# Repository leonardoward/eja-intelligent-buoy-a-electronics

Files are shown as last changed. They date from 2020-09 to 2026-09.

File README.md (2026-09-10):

# EJA Intelligent Buoy A - Electronic Design

EJA Intelligent Buoy A - Electronic Design - [2020 Hackaday Dream Team Challenge for Conservation X Labs](https://hackaday.io/project/173457-2020-hdp-dream-team-conservation-x-labs).

Buoy A is a 141.73 mm x 54.86 mm PCB that integrates 5 main modules (ESP32, LoRa, GPS, Motor Driver and GSM/GPRS).

This repository contains the KiCad design for the PCB of the Intelligent Buoy A. It also contains the 3D models used to visualize the design in the KiCad 3D viewer.

## Context

**EJA** is a pop‑up recovery buoy for lost fishing gear. A buoy sits on the seabed
attached to a trap or net; a scheduled timer (or a command over LoRa from the
[Onboard Gateway](https://github.com/leonardoward/eja-onboard-gateway-electronics))
releases it, it floats up, and its GPS position is reported so the gear can be
recovered. **Buoy A** is the fuller variant &mdash; it adds a **TB6612FNG** motor driver
for the release actuator and an optional **SIM7600 GSM/GPRS** shield for a cellular
uplink where there is coverage. It runs the
[Buoy firmware](https://github.com/leonardoward/eja-intelligent-buoy-b-firmware).
The single‑board successor that folds this whole system onto one PCB is
[EJA M](https://github.com/leonardoward/eja-m-pcb-design).

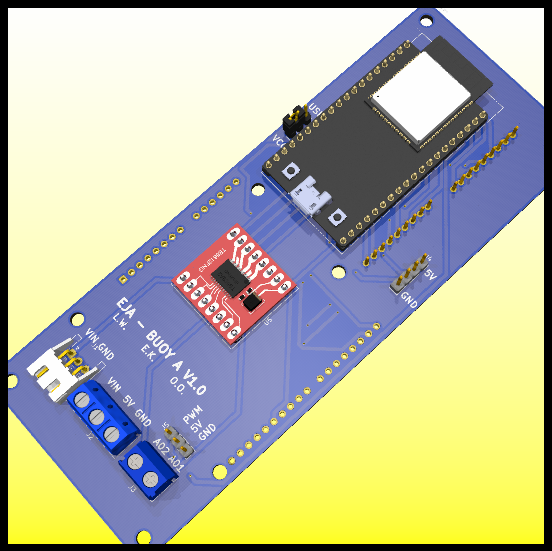
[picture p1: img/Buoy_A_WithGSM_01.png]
Front Layer PCB


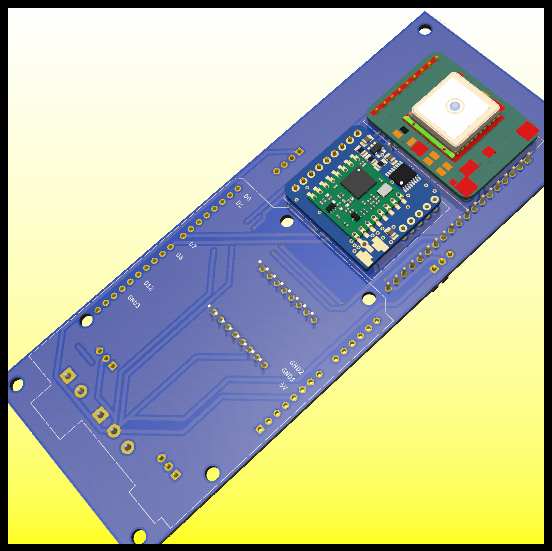
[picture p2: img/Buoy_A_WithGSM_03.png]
Back Layer PCB


## Main Components ##

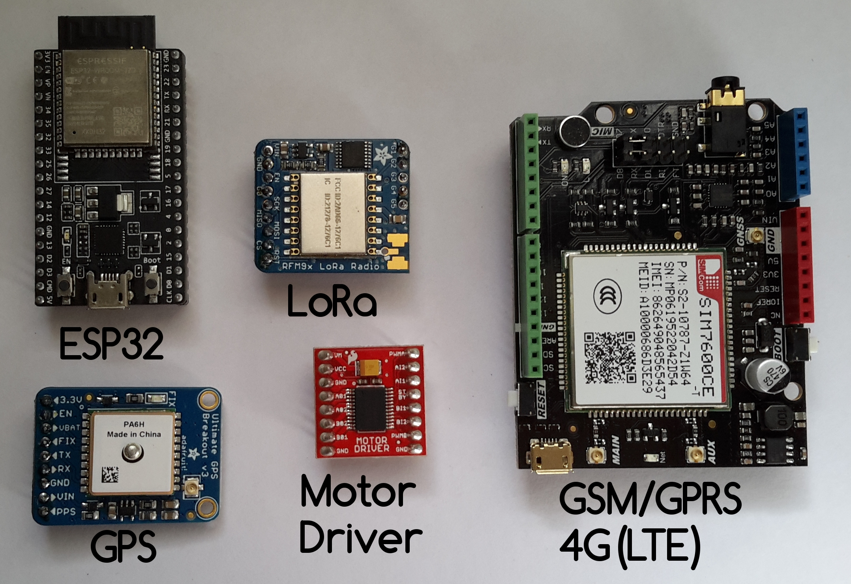
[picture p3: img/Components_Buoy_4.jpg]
Components


Sources:

- [ESP32-DEVKITC-32D](https://www.digikey.com/product-detail/es/espressif-systems/ESP32-DEVKITC-32D/1965-1000-ND/9356990)
- [RFM95W LoRa Radio](https://www.digikey.com/product-detail/es/adafruit-industries-llc/3072/1528-1667-ND/6005357)
- [TB6612FNG MOTOR DRIVER BOARD](https://www.digikey.com/product-detail/es/sparkfun-electronics/ROB-14450/1568-1755-ND/7915576)
- [Adafruit Ultimate GPS](https://www.digikey.com/product-detail/es/adafruit-industries-llc/746/1528-1153-ND/5353613)
- [SIM7600CE-T 4G(LTE) Arduino Shield](https://www.mouser.com/ProductDetail/DFRobot/TEL0124?qs=17u8i%2FzlE88MEbXRJuYFsA==)

## Schematic ##

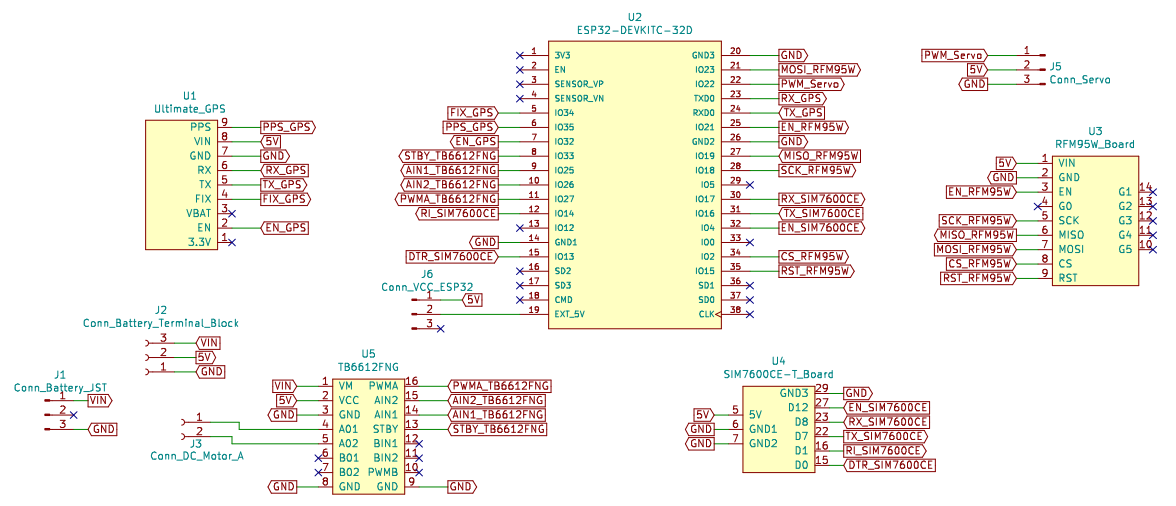
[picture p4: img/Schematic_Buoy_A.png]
Schematic


[For a detailed explanation of the schematic visit the following log.](https://hackaday.io/project/173457/log/181830-buoy-a-v10-schematic-and-pcb-design)

## PCB Layout ##

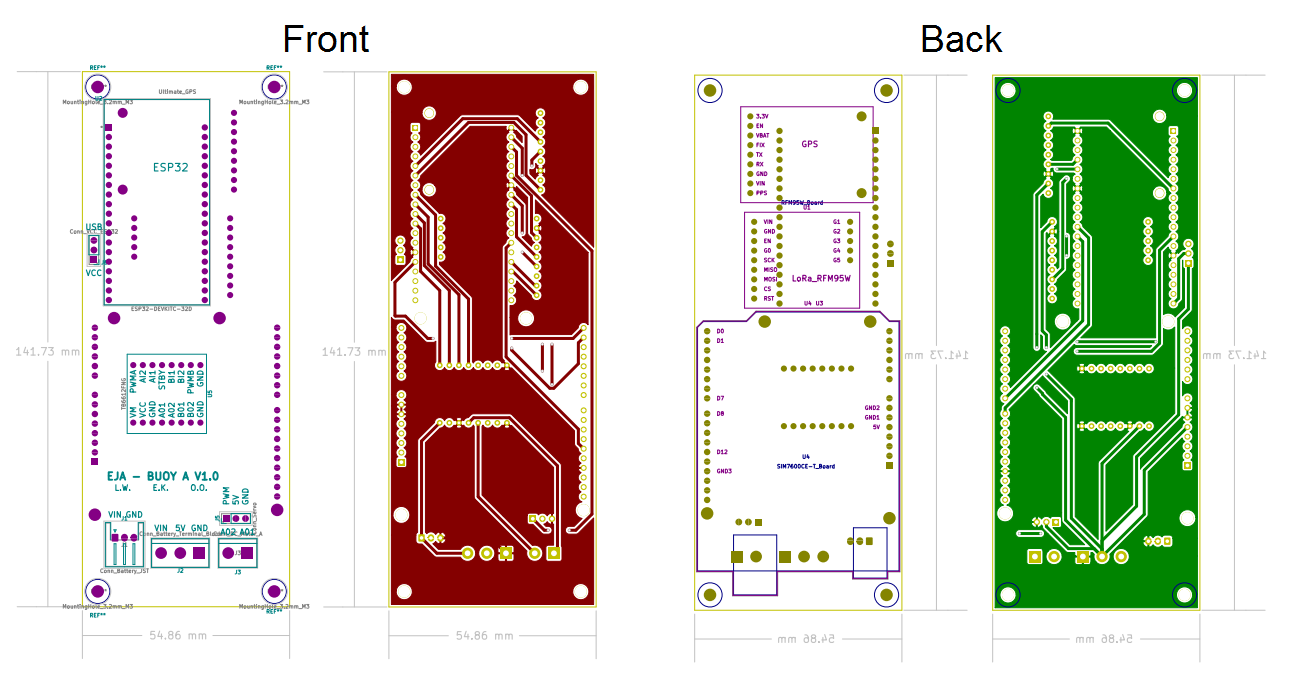
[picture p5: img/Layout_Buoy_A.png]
PCB Layout


## Assembly ##

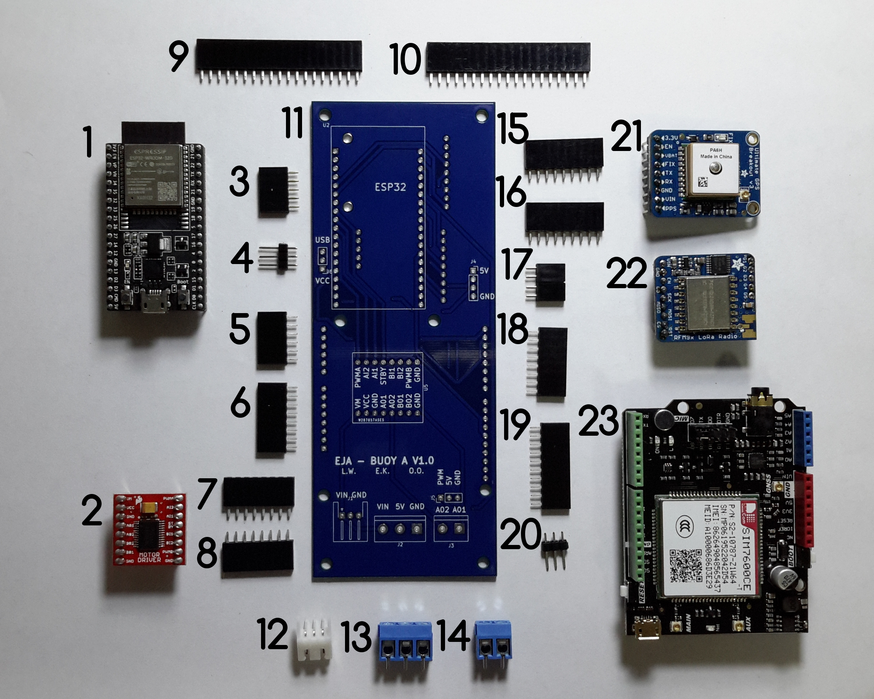
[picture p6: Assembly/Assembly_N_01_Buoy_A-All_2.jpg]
Assembly Guide


Components List:

1. [ESP32-DEVKITC-32D](https://www.digikey.com/product-detail/es/espressif-systems/ESP32-DEVKITC-32D/1965-1000-ND/9356990)
2. [TB6612FNG MOTOR DRIVER BOARD](https://www.digikey.com/product-detail/es/sparkfun-electronics/ROB-14450/1568-1755-ND/7915576)
3. [CONN HDR 5POS 0.1 GOLD PCB](https://www.digikey.com/product-detail/es/sullins-connector-solutions/PPTC051LFBN-RC/S6103-ND/807239)
4. [CONN HEADER VERT 3POS 2.54MM](https://www.digikey.com/product-detail/es/jst-sales-america-inc/S2B-XH-A-1-LF-SN/455-4226-ND/9961922)
5. [CONN HDR 6POS 0.1 TIN PCB](https://www.digikey.com/product-detail/es/sullins-connector-solutions/PPTC061LFBN-RC/S7004-ND/810145)
6. [CONN HDR 8POS 0.1 TIN PCB](https://www.digikey.com/product-detail/es/sullins-connector-solutions/PPTC081LFBN-RC/S7006-ND/810147)
7. [CONN HDR 8POS 0.1 TIN PCB](https://www.digikey.com/product-detail/es/sullins-connector-solutions/PPTC081LFBN-RC/S7006-ND/810147)
8. [CONN HDR 8POS 0.1 TIN PCB](https://www.digikey.com/product-detail/es/sullins-connector-solutions/PPTC081LFBN-RC/S7006-ND/810147)
9. [CONN HDR 19POS 0.1 TIN PCB](https://www.digikey.com/product-detail/es/sullins-connector-solutions/PPTC191LFBN-RC/S7017-ND/810157)
10. [CONN HDR 19POS 0.1 TIN PCB](https://www.digikey.com/product-detail/es/sullins-connector-solutions/PPTC191LFBN-RC/S7017-ND/810157)
11. PCB Buoy A V1.0
12. [CONN HEADER R/A 3POS 2.5MM](https://www.digikey.com/product-detail/es/jst-sales-america-inc/S3B-XH-A-1-LF-SN/455-2954-ND/1556255)
13. [TERM BLK 3P SIDE ENT 5.08MM PCB](https://www.digikey.com/product-detail/es/on-shore-technology-inc/OSTTC032162/ED2610-ND/614559)
14. [TERM BLK 2P SIDE ENT 5.08MM PCB](https://www.digikey.com/product-detail/es/on-shore-technology-inc/OSTTC022162/ED2609-ND/614558)
15. [CONN HDR 9POS 0.1 GOLD PCB](https://www.digikey.com/product-detail/es/sullins-connector-solutions/PPPC091LFBN-RC/S7042-ND/810181)
16. [CONN HDR 9POS 0.1 GOLD PCB](https://www.digikey.com/product-detail/es/sullins-connector-solutions/PPPC091LFBN-RC/S7042-ND/810181)
17. 2 [CONN HDR 2POS 0.1 GOLD PCB](https://www.digikey.com/product-detail/es/sullins-connector-solutions/PPPC021LFBN-RC/S7035-ND/810174)
18. [CONN HDR 9POS 0.1 GOLD PCB](https://www.digikey.com/product-detail/es/sullins-connector-solutions/PPPC091LFBN-RC/S7042-ND/810181)
19. [CONN HDR 10POS 0.1 TIN PCB](https://www.digikey.com/product-detail/es/sullins-connector-solutions/PPTC101LFBN-RC/S7008-ND/810149)
20. [CONN HEADER VERT 3POS 2.54MM](https://www.digikey.com/product-detail/es/jst-sales-america-inc/S2B-XH-A-1-LF-SN/455-4226-ND/9961922)
21. [Adafruit Ultimate GPS](https://www.digikey.com/product-detail/es/adafruit-industries-llc/746/1528-1153-ND/5353613)
22. [RFM95W LoRa Radio](https://www.digikey.com/product-detail/es/adafruit-industries-llc/3072/1528-1667-ND/6005357)
23. [SIM7600CE-T 4G(LTE) Arduino Shield](https://www.mouser.com/ProductDetail/DFRobot/TEL0124?qs=17u8i%2FzlE88MEbXRJuYFsA==)

[For a detailed Bill of Materials visit the following log.](https://hackaday.io/project/173457/log/183798-buoy-a-v10-bill-of-materials)

[For a detailed explanation about the soldering and assembly procedure visit the following log.](https://hackaday.io/project/173457/log/183738-buoy-a-v10-assembly)

## Wiring Diagrams ##

The following diagrams present the physical connections of the different boards and components of the Buoy A V1.0.

### Battery Management ###

The original design of the board considered the following components:

- Battery (5V < Voltage < 15V)
- PCB Board Buoy A V1.0
- Buck Converter
- Switch
- Extra capacitor

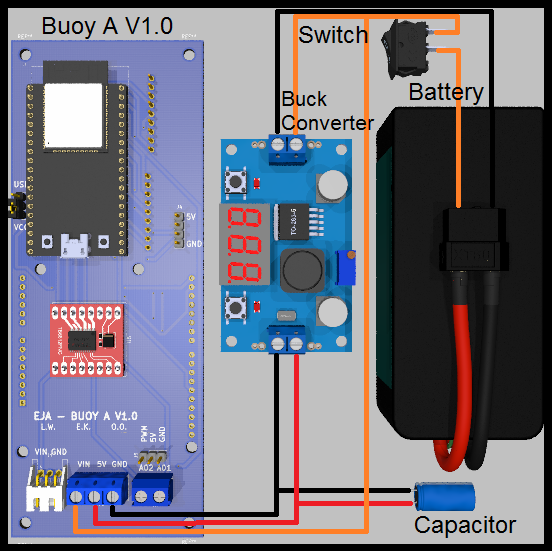
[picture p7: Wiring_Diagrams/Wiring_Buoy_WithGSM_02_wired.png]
Buck Converter


Similar to Buoy B, there is an alternative for the battery management, is possible to provide the required voltages with a boost converter and a 3.7V Battery, like the following example:

- 3.7V 1 Cell Battery
- PCB Board Buoy A V1.0
- Boost Converter
- Micro USB Breakout Board
- Switch
- Extra capacitor
- JST-XH 2 Pos female connector and a JST-XH 2 Pos male connector
- 5V Charger (only used to charge the battery)

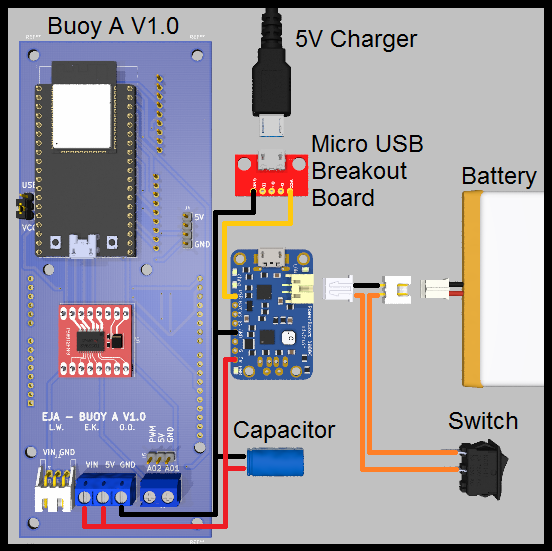
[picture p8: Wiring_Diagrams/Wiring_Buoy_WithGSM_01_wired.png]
Boost Converter


This alternative is valid and possible, but is not ideal for longer working time (compared to the first one). It is important to consider the efficiency of the boost converter. The selected boost converter will have a voltage drop at a current higher than 500mA, that should be taken into consideration.

### Motors ###

The board was designed to handle 2 different types of motors, those are:

- Servo Motor

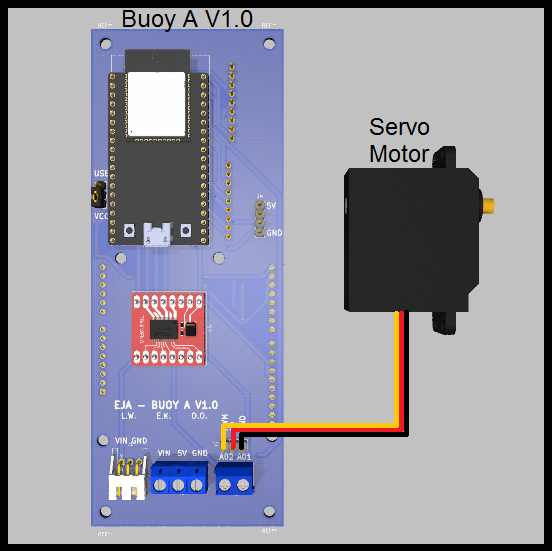
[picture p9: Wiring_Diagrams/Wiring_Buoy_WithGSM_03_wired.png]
Servo Motor


- DC Motor (using the driver TB6612FNG)

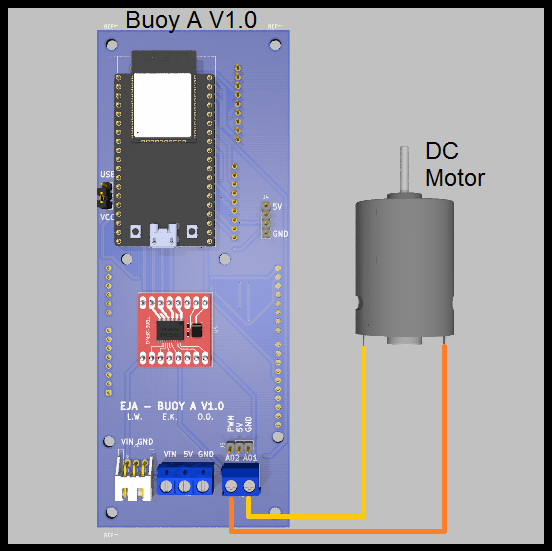
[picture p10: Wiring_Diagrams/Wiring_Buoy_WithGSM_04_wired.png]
DC Motor


[For more information about the wiring diagrams and the project visit the following log.](https://hackaday.io/project/173457/log/182856-buoy-a-v10-wiring-diagrams)

## Future improvements ##

[For more information about the recommended future improvements for the electronic design visit the following log.](https://hackaday.io/project/173457/log/183807-future-improvements-pcb-design)

## Repository Layout

```
Buoy_WithGSM.sch / .kicad_pcb        KiCad 5 project (schematic + board)
Buoy_WithGSM.pro / .net              project + netlist
Symbols/  Footprints/  3D/  step/    project-local libraries and 3D models
Gerber/                              fabrication output
Assembly/                            assembly reference photos
Wiring_Diagrams/                     board-to-component wiring (battery, servo, DC motor)
pdf/  plot/                          exported schematic / layout PDFs
img/                                 renders and photos used in this README
LICENSE                              Apache 2.0
```

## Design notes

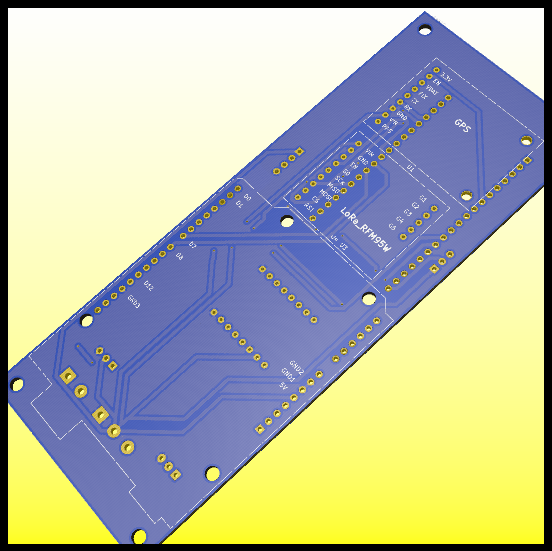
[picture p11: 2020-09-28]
img/Buoy_A_WithGSM_04.png

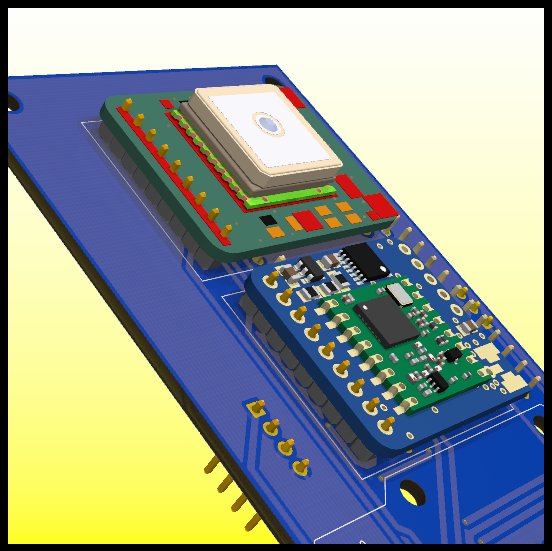
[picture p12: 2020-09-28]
img/Buoy_A_WithGSM_05.png

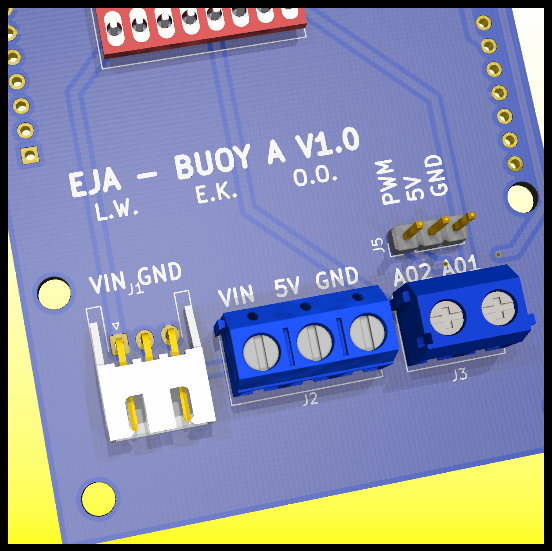
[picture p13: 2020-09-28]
img/Buoy_A_WithGSM_08.png

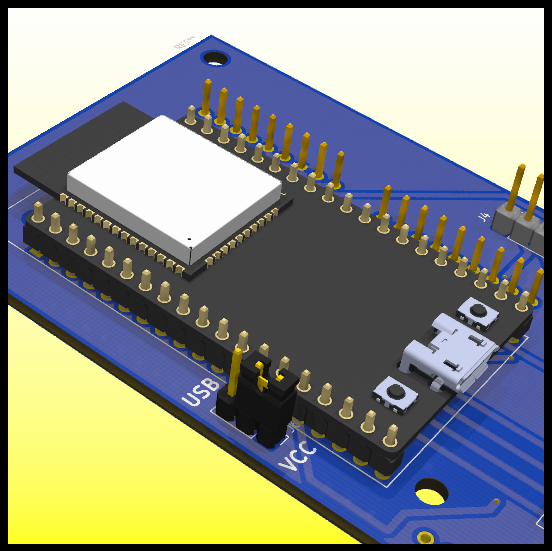
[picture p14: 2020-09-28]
img/Buoy_A_WithGSM_07.png

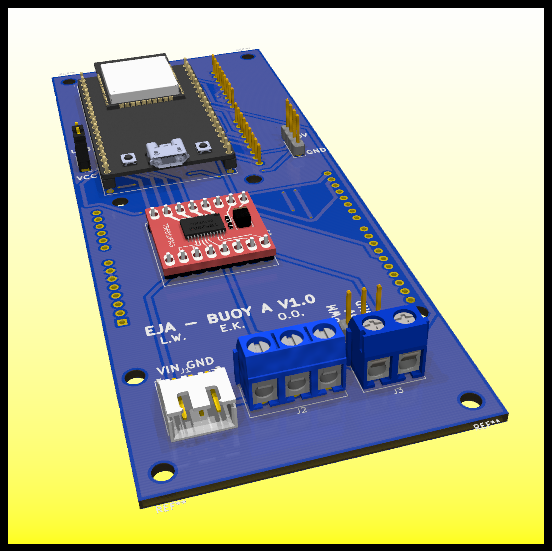
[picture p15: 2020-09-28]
img/Buoy_A_WithGSM_09.png

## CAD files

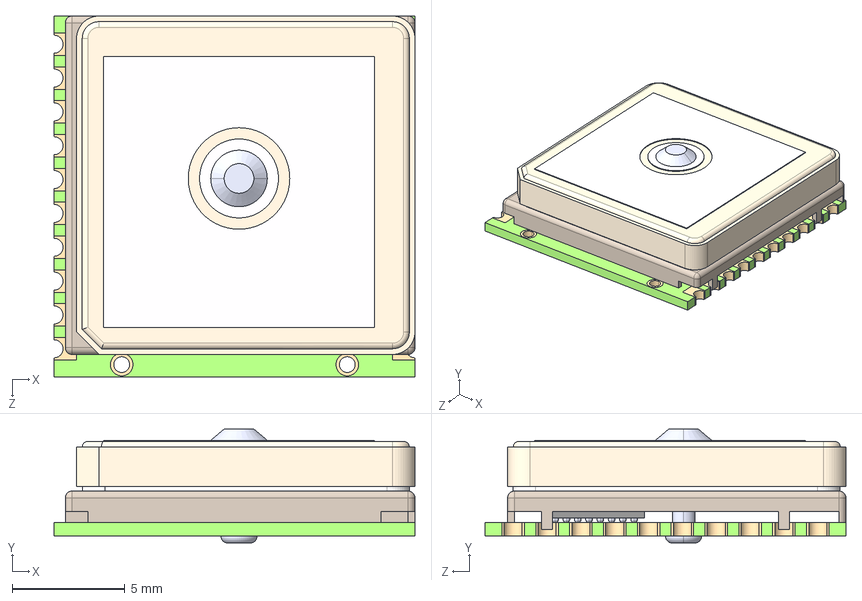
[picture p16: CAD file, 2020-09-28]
3D/PA6H Assembly.STEP
16.0 x 5.05 x 16.0 mm
PCB
VFBGA-64
RF Shield
Adhesive Pad
Ceramic Antenna
Rivet

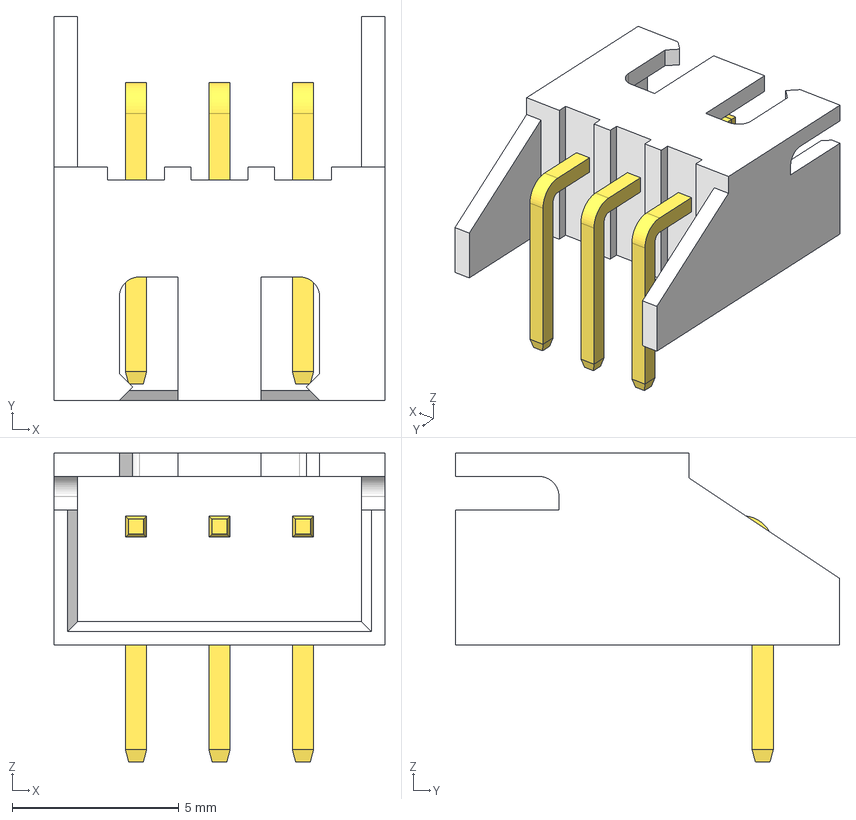
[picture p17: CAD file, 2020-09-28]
3D/S3B-XH-A.step
9.90 x 11.5 x 9.25 mm

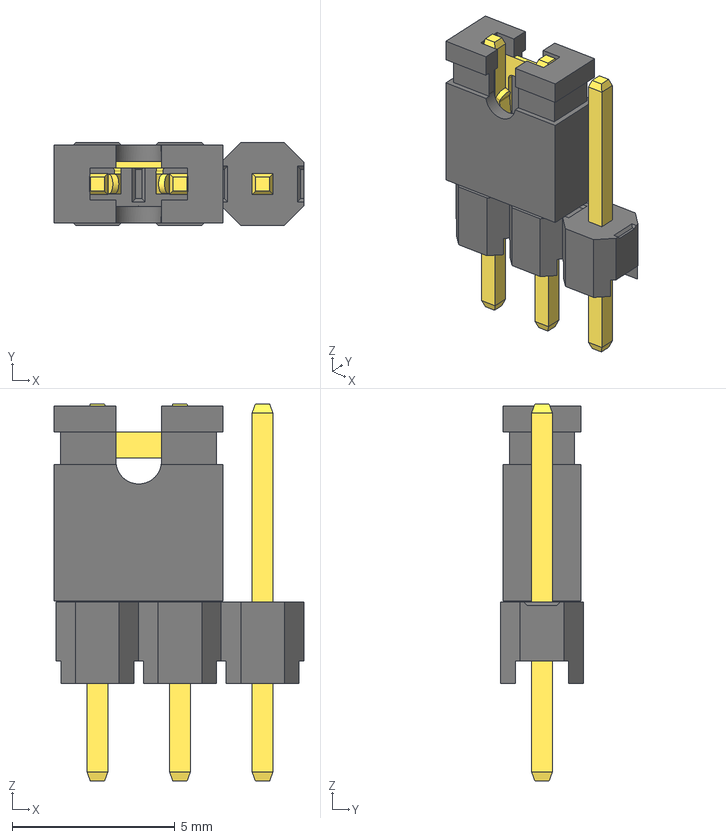
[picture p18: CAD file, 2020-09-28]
3D/Jumper3.step
7.68 x 2.54 x 11.6 mm

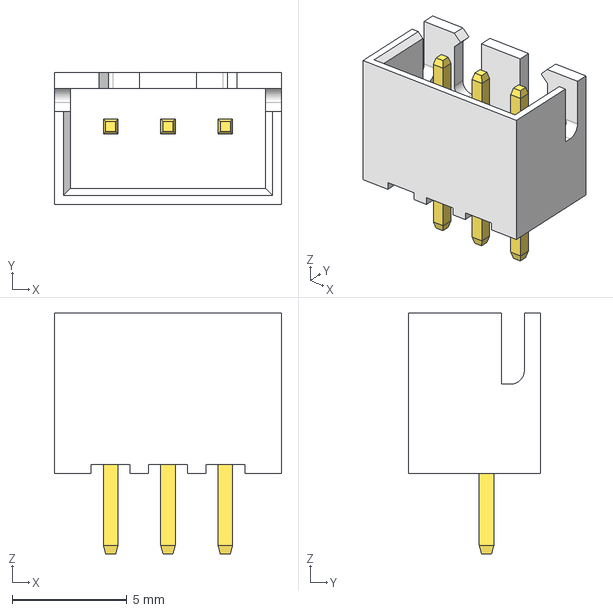
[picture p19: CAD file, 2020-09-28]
3D/B3B-XH-A.step
9.90 x 5.75 x 10.5 mm

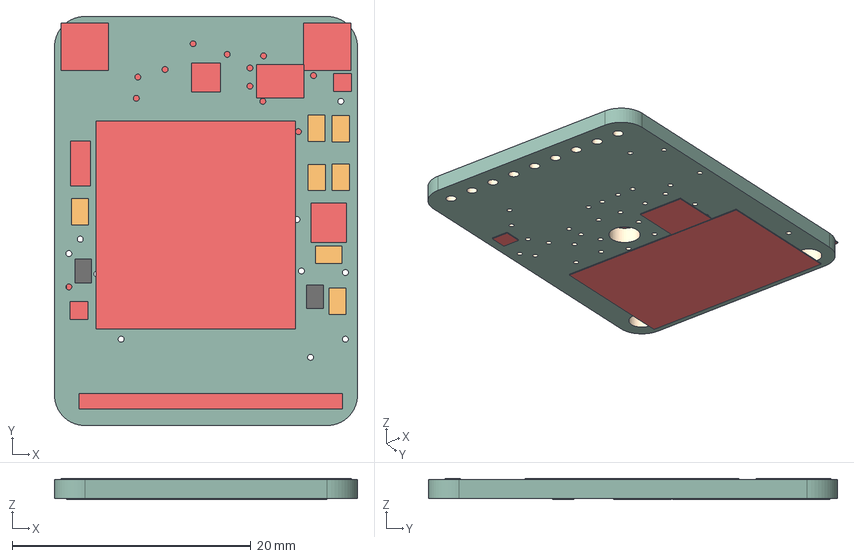
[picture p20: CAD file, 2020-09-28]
3D/Adafruit Ultimate GPS.step
25.4 x 34.3 x 1.77 mm
Board
FGPMMOPA6H
MIC5225-3.3
RED
10K x 7
MOUNTINGHOLE2.5 x 2
CUS520 x 2
CR1220
FIDUCIAL"" x 2
ADAFRUIT_2.5MM
U.FL
1X09_ROUND_70
PCBFEAT-REV-040
ADAFRUIT_5MM

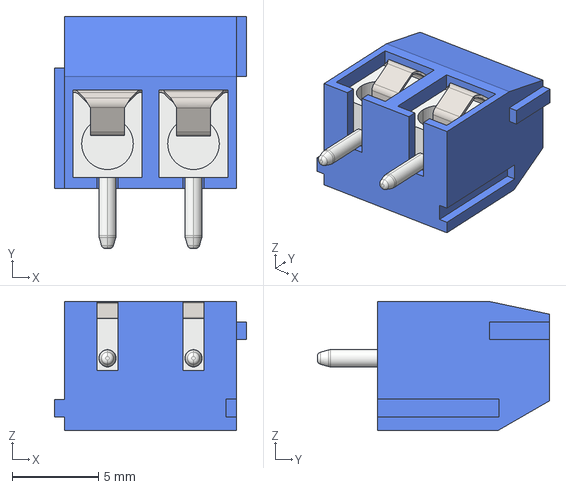
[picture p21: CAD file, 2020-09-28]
3D/TE_1776244-2.STEP
11.2 x 13.5 x 7.50 mm

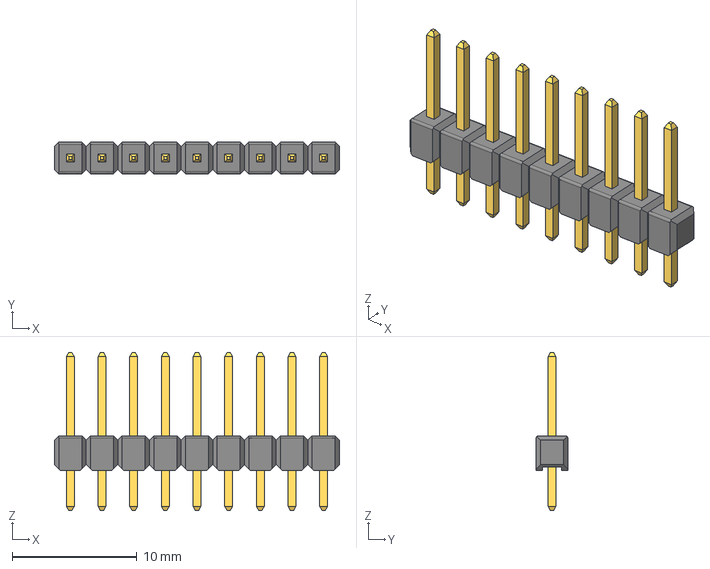
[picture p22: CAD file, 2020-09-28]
3D/Pin Header 1x9 TH Pitch 2.54mm.stp
22.9 x 2.54 x 12.7 mm

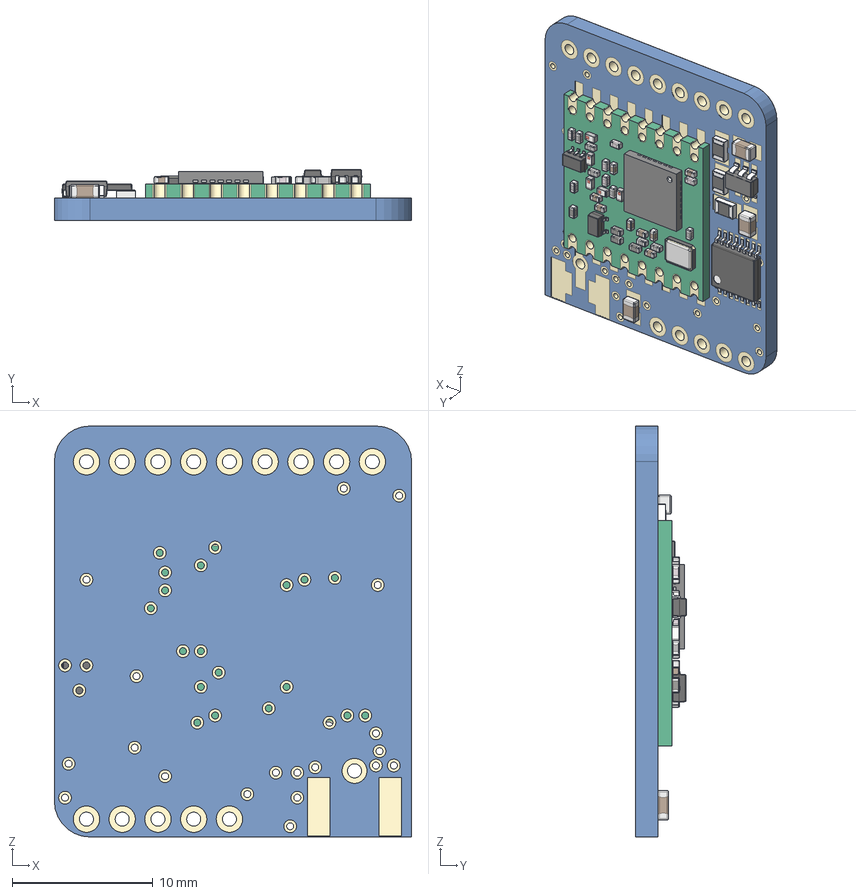
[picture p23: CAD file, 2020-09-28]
3D/RFM95W v5.step
25.4 x 3.63 x 29.2 mm
QFN 28 v2
SMD Crystal v1
CAP 0403 v1 x 8
CAP Ceramic 0403 v1 x 8
Res 0403 v1 x 4
CAP ML 0403 v1 x 5
SOT-323 v1
Inductor SMD 0403 v1 x 5
SOT-363 v1
SOT23-5
CAP 0805 T095 x 2
CAP 0805 T075
TSSOP16
RES 0805 x 3

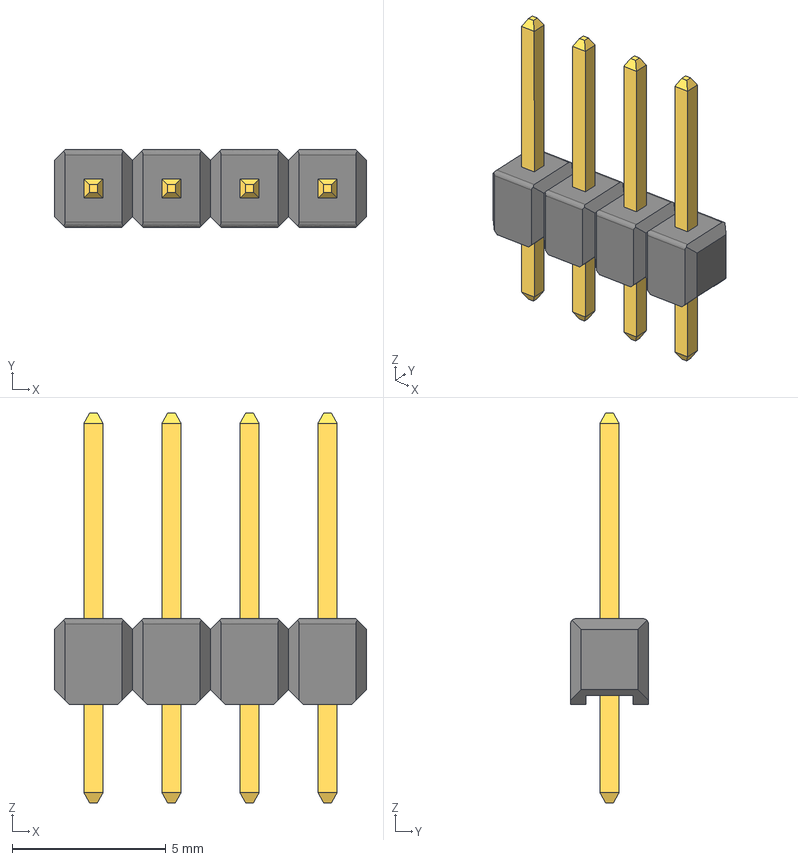
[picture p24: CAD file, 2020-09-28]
3D/Pin Header 1x4 TH Pitch 2.54mm.stp
10.2 x 2.54 x 12.7 mm

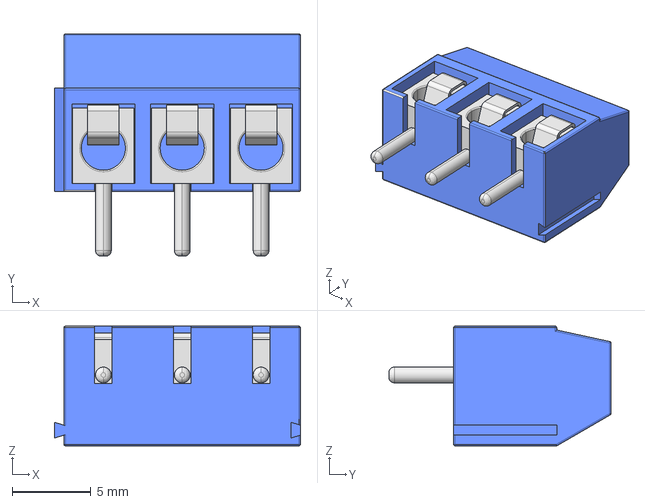
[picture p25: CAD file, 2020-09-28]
3D/terminal_block_tb5p-3p_p5_l15_w7-6_h10.stp
15.6 x 14.1 x 7.60 mm

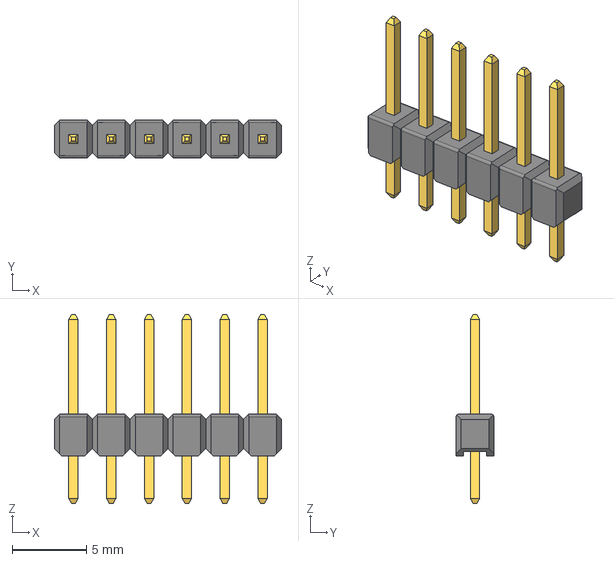
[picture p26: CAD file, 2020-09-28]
3D/Pin Header 1x6 TH Pitch 2.54mm.stp
15.2 x 2.54 x 12.7 mm

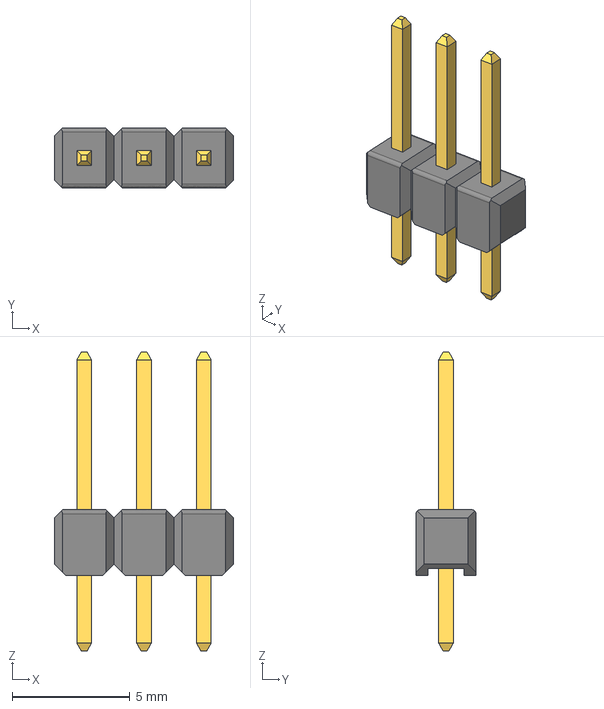
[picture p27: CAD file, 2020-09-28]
3D/Pin Header 1x3 TH Pitch 2.54mm.stp
7.62 x 2.54 x 12.7 mm

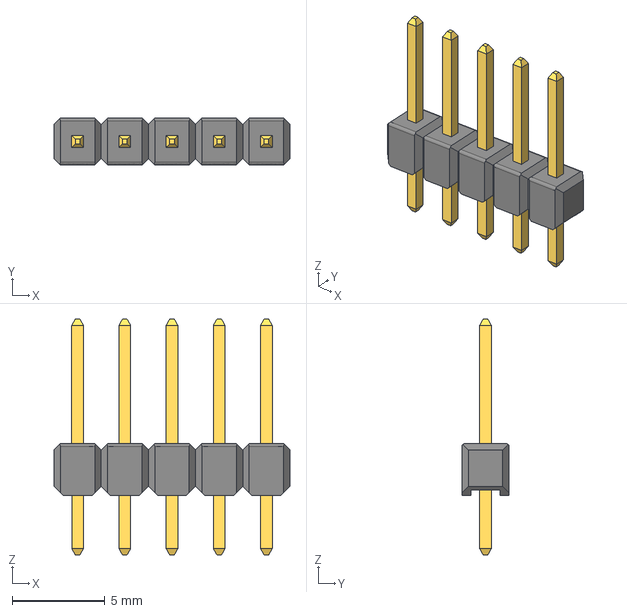
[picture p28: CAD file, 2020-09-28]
3D/Pin Header 1x5 TH Pitch 2.54mm.stp
12.7 x 2.54 x 12.7 mm

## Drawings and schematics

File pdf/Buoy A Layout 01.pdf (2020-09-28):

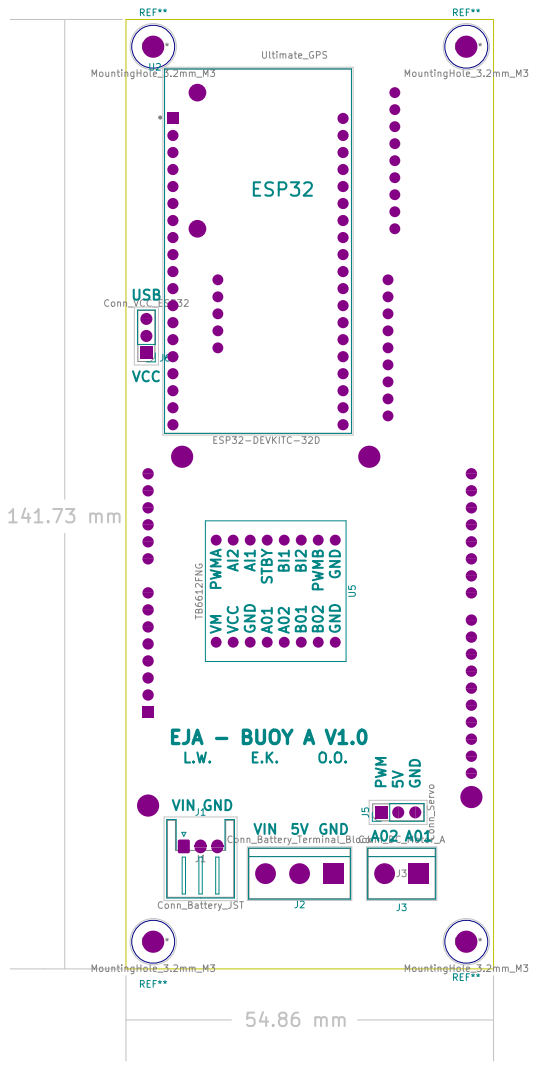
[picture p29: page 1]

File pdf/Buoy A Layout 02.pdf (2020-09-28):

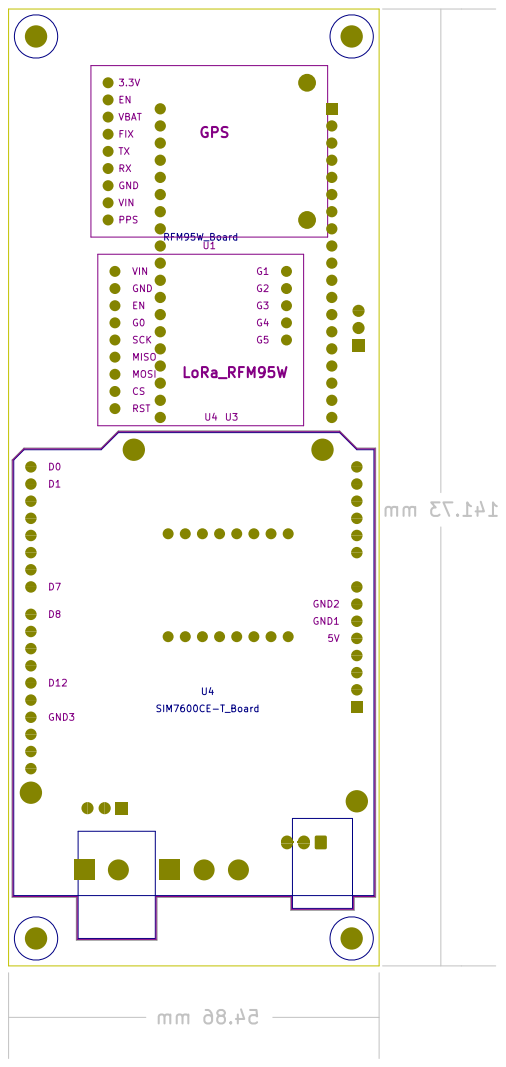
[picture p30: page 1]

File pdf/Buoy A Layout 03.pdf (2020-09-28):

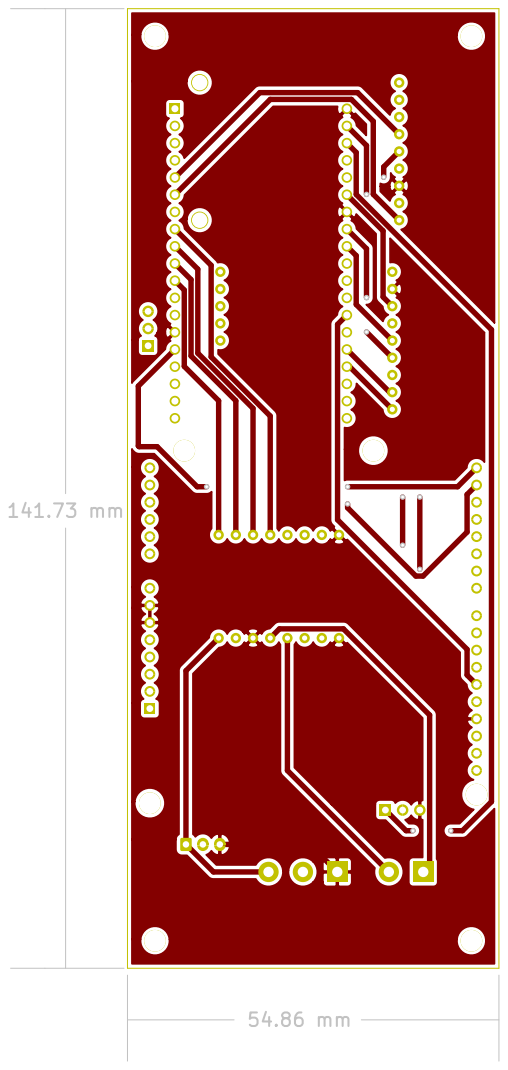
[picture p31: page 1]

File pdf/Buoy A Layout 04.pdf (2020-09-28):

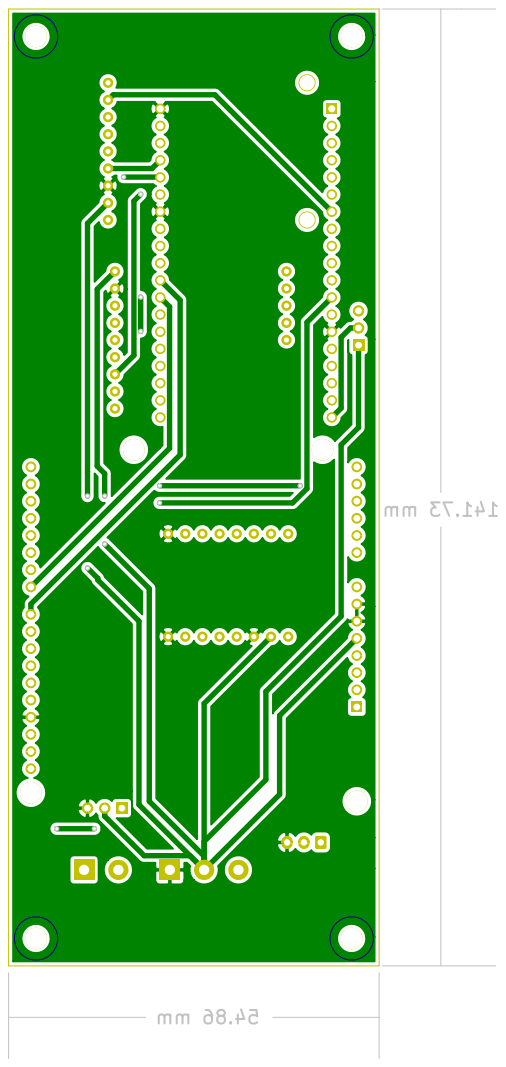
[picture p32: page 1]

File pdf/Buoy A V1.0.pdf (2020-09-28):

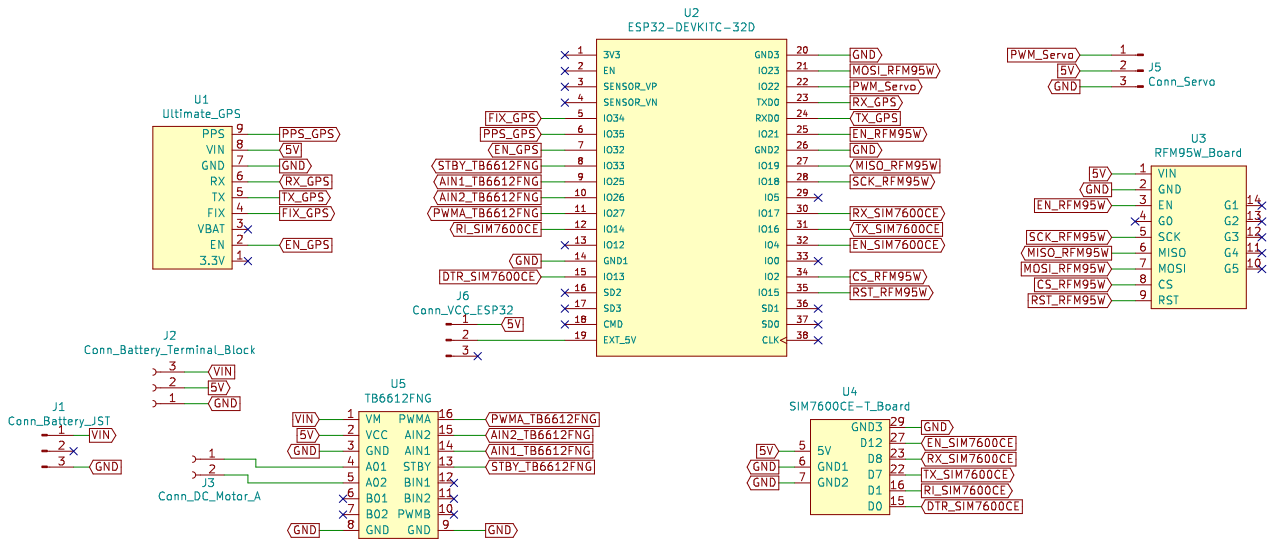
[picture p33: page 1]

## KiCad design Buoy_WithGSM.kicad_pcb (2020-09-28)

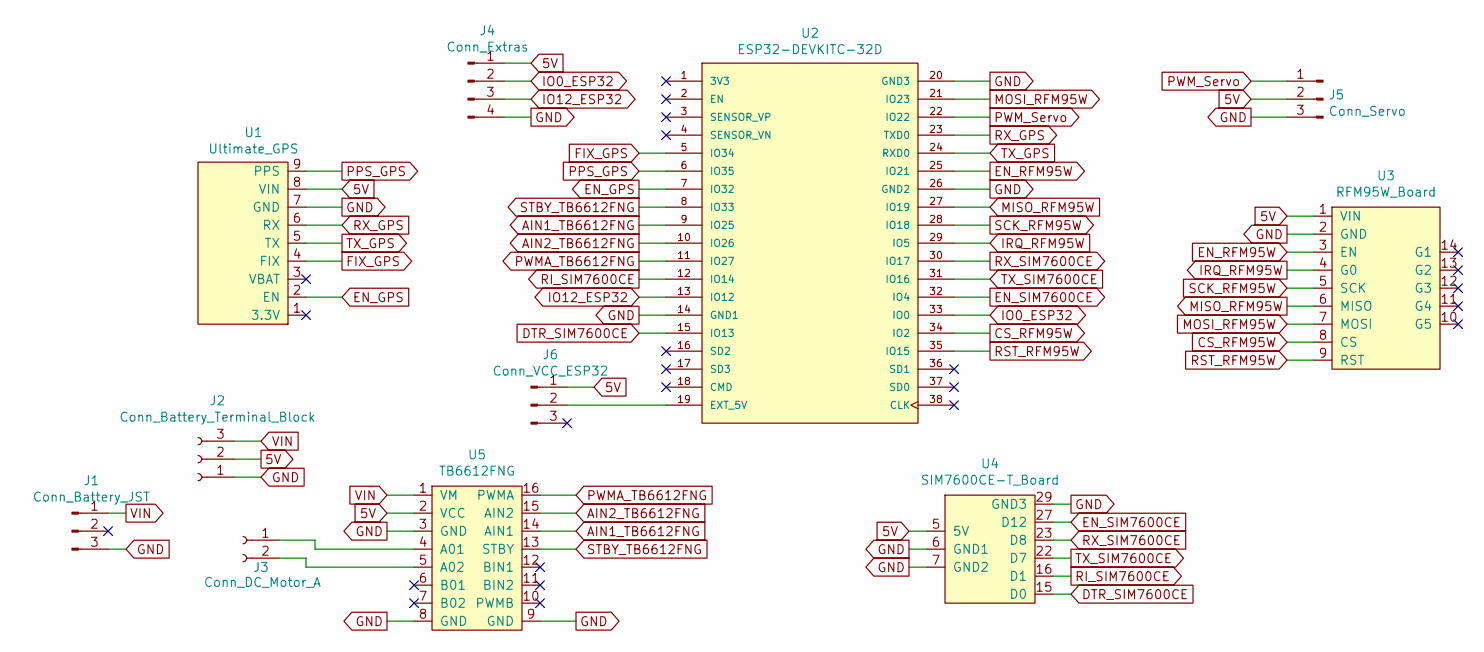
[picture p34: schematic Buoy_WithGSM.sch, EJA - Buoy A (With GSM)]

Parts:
J1: Conn_Battery_JST; JST_XH_S3B-XH-A-1_1x03_P2.50mm_Horizontal
J2: Conn_Battery_Terminal_Block; TerminalBlock_bornier-3_P5.08mm
J3: Conn_DC_Motor_A; TerminalBlock_bornier-2_P5.08mm
J4: Conn_Extras; PinSocket_1x04_P2.54mm_Vertical
J5: Conn_Servo; PinHeader_1x03_P2.54mm_Vertical
J6: Conn_VCC_ESP32; PinHeader_1x03_P2.54mm_Vertical
U1: Ultimate_GPS
U2: ESP32-DEVKITC-32D; MODULE_ESP32-DEVKITC-32D
U3: RFM95W_Board; RFM95W-Board
U4: SIM7600CE-T_Board
U5: TB6612FNG

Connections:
5V: J2.2, J4.1, J5.2, J6.1, U1.8 (VIN), U3.1 (VIN), U4.5 (5V), U5.2 (VCC)
AIN1_TB6612FNG: U2.9 (IO25), U5.14 (AIN1)
AIN2_TB6612FNG: U2.10 (IO26), U5.15 (AIN2)
CS_RFM95W: U2.34 (IO2), U3.8 (CS)
DTR_SIM7600CE: U2.15 (IO13), U4.15 (D0)
EN_GPS: U1.2 (EN), U2.7 (IO32)
EN_RFM95W: U2.25 (IO21), U3.3 (EN)
EN_SIM7600CE: U2.32 (IO4), U4.27 (D12)
FIX_GPS: U1.4 (FIX), U2.5 (IO34)
GND: J1.3, J2.1, J4.4, J5.3, U1.7 (GND), U2.14 (GND1), U2.20 (GND3), U2.26 (GND2), U3.2 (GND), U4.6 (GND1), U4.7 (GND2), U4.29 (GND3), U5.3 (GND), U5.8 (GND), U5.9 (GND)
IO0_ESP32: J4.2, U2.33 (IO0)
IO12_ESP32: J4.3, U2.13 (IO12)
IRQ_RFM95W: U2.29 (IO5), U3.4 (G0)
MISO_RFM95W: U2.27 (IO19), U3.6 (MISO)
MOSI_RFM95W: U2.21 (IO23), U3.7 (MOSI)
unnamed: J3.1, U5.4 (A01)
unnamed: J3.2, U5.5 (A02)
unnamed: J6.2, U2.19 (EXT_5V)
PPS_GPS: U1.9 (PPS), U2.6 (IO35)
PWMA_TB6612FNG: U2.11 (IO27), U5.16 (PWMA)
PWM_Servo: J5.1, U2.22 (IO22)
RI_SIM7600CE: U2.12 (IO14), U4.16 (D1)
RST_RFM95W: U2.35 (IO15), U3.9 (RST)
RX_GPS: U1.6 (RX), U2.23 (TXD0)
RX_SIM7600CE: U2.30 (IO17), U4.23 (D8)
SCK_RFM95W: U2.28 (IO18), U3.5 (SCK)
STBY_TB6612FNG: U2.8 (IO33), U5.13 (STBY)
TX_GPS: U1.5 (TX), U2.24 (RXD0)
TX_SIM7600CE: U2.31 (IO16), U4.22 (D7)
VIN: J1.1, J2.3, U5.1 (VM)

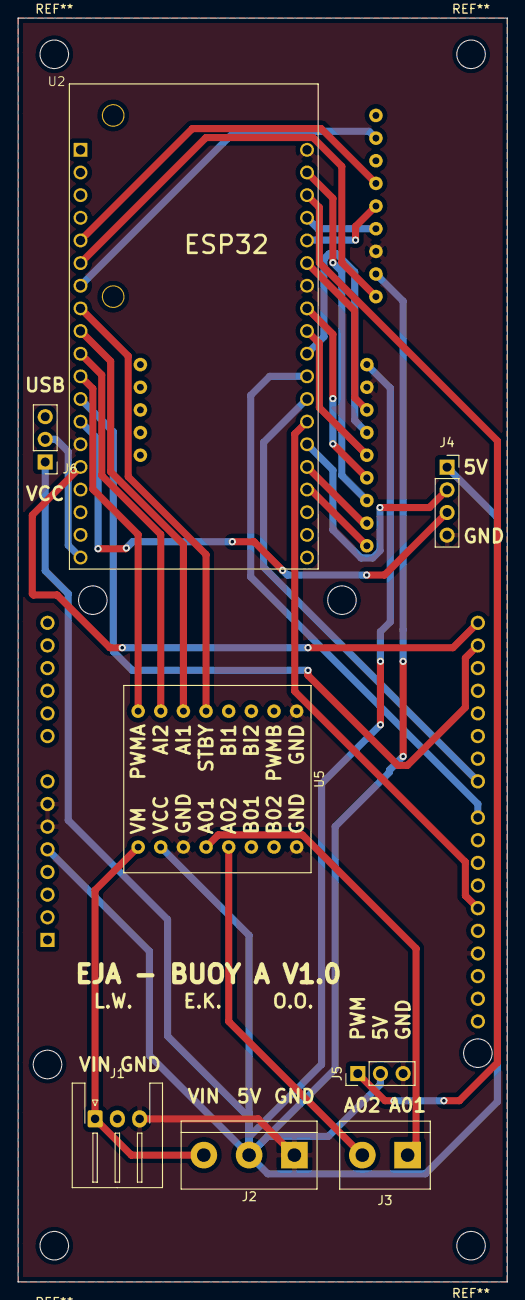
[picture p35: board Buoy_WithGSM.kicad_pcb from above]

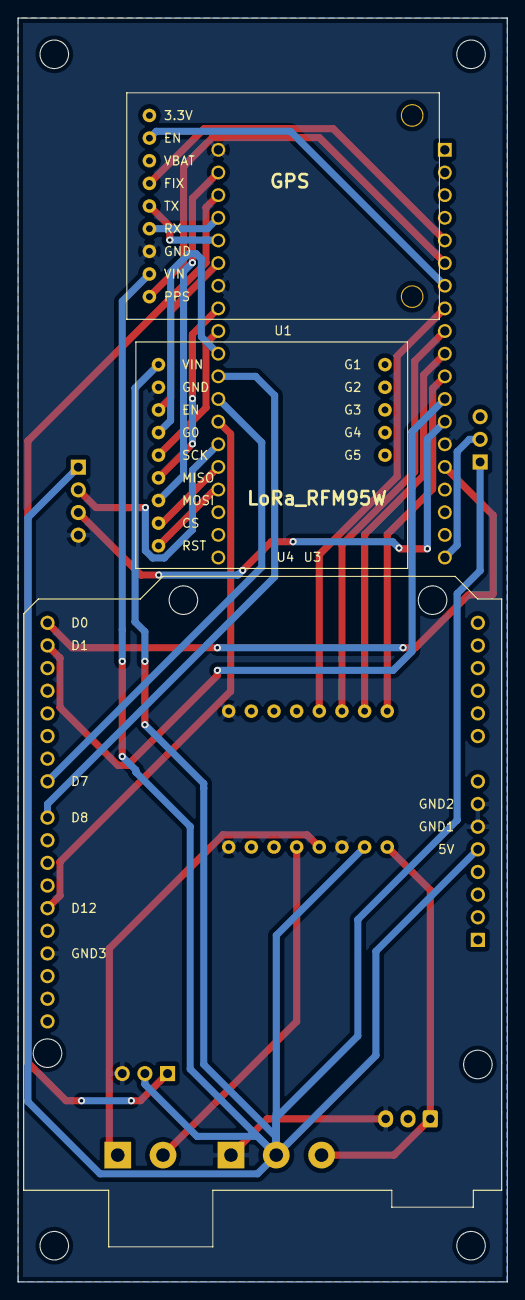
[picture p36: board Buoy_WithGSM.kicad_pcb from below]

Board: 2 copper layers, 54.9 x 141.7 mm, 11 parts (2 on the bottom side), 30 nets.

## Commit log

2020-09-28 Added KiCad design
    [Adafruit Ultimate GPS.step, B3B-XH-A.step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]
2020-09-28 Added wiring diagrams and assembly guide
2020-09-28 Added PCB image
2020-09-28 Changed pcb image
